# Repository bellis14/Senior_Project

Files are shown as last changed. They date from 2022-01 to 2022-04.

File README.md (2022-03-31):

# Senior Project - Personal Camerabot

* [Android Studio Setup and App Installation](https://github.com/bellis14/Senior_Project/blob/main/SoftwareSetup.md)
* [Project Specifications](https://github.com/bellis14/Senior_Project/blob/main/ProjectRequirements.md)
* [Future Development](https://github.com/bellis14/Senior_Project/blob/main/Future%20Developments.md)

### Useful Links

* [The code for the ios app and android app were found from here.](https://github.com/googlesamples/mlkit)

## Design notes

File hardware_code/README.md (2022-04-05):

# Hardware code

## Description
* The AutoCameraMan arduino file is the code that is downloaded onto the ESP32 to run the project. This file is used to broadcoast bluetooth classic to an android phone. This code successfully connects to the AutoCameraMan app and will receive motor instructions when the app is set to facial or pose detection. When the instructions are received the code will function with good motor control. iPhone devices can also connect to bluetooth classic. 
* The BLE_Server file is used to broadcoast a bluetooth low energy signal. iPhone and Android can connect to both bluetooth low energy (BLE) and bluetooth classic. Bluetooth classic is easier to implement than BLE.   

## Research 
* [Bluetooth/ESP32 Research](https://docs.google.com/document/d/1fT-Hv9j815ZINsvS9MvsHoMjV4GRWzmnJF0-fi07Mzs/edit)
* [Servo DS3225 spec sheet](https://dsservo.com/en/d_file/RDS3225%20datasheet.pdf)
* [Wiring Diagram of board and servos. Scroll down till you see it](https://create.arduino.cc/projecthub/zee9309/presentation-slide-switcher-bot-36b8f6)

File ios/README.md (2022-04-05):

# Description
The iphone portion of the project has been nearly untouched. We were able to build and run the project provided by googles ML kit but we haven't added any additional functionality. We found the resources that will be used to implement bluetooth, which can be found below in the Bluetooth Resources section, but we never integrated it into the app or even tested the bluetooth code provided by apple. The instructions for building and running the app are provided below in the Steps for setting up development on mac computer section. After you get the app running on your iphone you can start adding the other functionalities. 

# Setting up for Development 
We did the development for the iphone app on xcode which requires macOS. If you don't have a mac computer then you can either set up a virtual machine using virtualbox or VMware workstation. You can also attempt to dual boot macOS onto the computer you are currently using. You just need to make sure your laptop meets the requirements for this option. The other option is to use the mac lab down in the library. There is a way to configure virtualbox and VMware to perform more smoothly but when we attempted to use it the performance was really bad in terms of their being lag. You would try to move your mouse somewhere and it would take a solid five seconds to move. The drawback of using the mac lab is you can't use sudo commands to download stuff. If you need to download something you will have to find a work around that doesn't require sudo. As of now the IT department has revoked admin access which means you can't download xcode. It is currently downloaded on computer 4 in the mac lab if you want to use that one. That is the computer that was used for development.

## Steps for setting up development on mac computer
At the end of this setup you should be able to build and run the app on your iphone device. This means you are ready to begin adding the functionality of bluetooth. There is a link down below in the section labeled Bluetooth Resources. Go to the link in that section and hit the download button. This will download the code that apple offers to connect to bluetooth classic devices.  
* Download Xcode
* Download cocoapods. Use homebrew not gem.
  * Download Homebrew with these commands. You can find the same commands [here](https://docs.brew.sh/Installation#untar-anywhere)
    * mkdir homebrew && curl -L https://github.com/Homebrew/brew/tarball/master | tar xz --strip 1 -C homebrew
    * Add the path: export PATH="/Users/coolasacucumber/Downloads/homebrew/bin:$PATH" (You will have to run this command any time you want to run pod install and you closed the terminal)
    * The path above will be different for you. I decided to make the homebrew directory in the downloads folder. 
    * eval "$(homebrew/bin/brew shellenv)"
    * brew update --force --quiet
    * chmod -R go-w "$(brew --prefix)/share/zsh"
  * brew install cocoapods (This will take forever just fyi)
* Use cocoapods to import the dependencies in the Podfile
  * Clone the senior project repository into your workspace
  * Change into the ios directory of the repository.
  * run the command: pod install
* Setting up your iphone device
  * Do not use the iOS simulators if you are using M1 chip mac computers. Feel free to try it. If it works great!
  * Follow this [video](https://www.youtube.com/watch?v=bqh6YaMxgbE) setting up your iphone device. 
  * If after setting up the device you get this error when trying to run the app: 
  
     "Showing Recent Messages Failed to register bundle identifier: The app identifier "com.google.mlkit.quickstart.VisionExample" cannot be registered to your development team because it is not available. Change your bundle identifier to a unique string to try again." 
  
     then you need to go into the targets and select the Signings and Capabilities tab and change the Build Identifier from com.google.mlkit.quickstart.VisionExample to something different. I changed it to com.google.mlkit.quickstart.VisionExample222 and hit the try again button. After that it worked for me and then I was able to finish setting up the iphone device by going into the iphones settings >general>VPN & Device Management and then selecting the developer app as was mentioned in the above video. After this last step you should be able to run the app successfully.

## Debugging for setting up development on mac lab computers
https://alexandernadein.medium.com/undefined-symbols-and-where-to-find-them-b98f16f5f805
https://githubhot.com/repo/googlesamples/mlkit/issues/398
https://developer.apple.com/forums/thread/130493
https://developer.apple.com/forums/thread/130493

## Setting up virtual machine
* [iOS development setup using a virtual machine on VMware workstation](https://www.youtube.com/watch?v=-5FpROxjHsw)

# Bluetooth Resources
* Download [this](https://developer.apple.com/documentation/corebluetooth/using_core_bluetooth_classic). Its apples code for connecting bluetooth devices.

# ML Kit Vision Quickstart Sample App

## Introduction

This ML Kit Vision iOS Quickstart app demonstrates how to use and integrate various vision based ML Kit features into your app.

## Feature List

Features that are included in this demo app:
* [Object Detection](https://developers.google.com/ml-kit/vision/object-detection/ios) - Detect, track, and classify objects in real time and static images
* [Custom Object Detection (Birds)](https://developers.google.com/ml-kit/vision/object-detection/custom-models/ios) - Detect, track, and classify birds with a custom TensorFlow Lite model
* [Face Detection](https://developers.google.com/ml-kit/vision/face-detection/ios) - Detect faces in real time and static images
* [Text Recognition](https://developers.google.com/ml-kit/vision/text-recognition/v2/ios) - Recognize text in real time and static images
* [Barcode Scanning ](https://developers.google.com/ml-kit/vision/barcode-scanning/ios)- Scan barcodes in real time and static images
* [Image Labeling](https://developers.google.com/ml-kit/vision/image-labeling/ios) - Label images in real time and static images
* [Custom Image Labeling (Birds)](https://developers.google.com/ml-kit/vision/image-labeling/custom-models/ios) - Label images of birds with a custom TensorFlow Lite model
* [Pose Detection](https://developers.google.com/ml-kit/vision/pose-detection/ios) - Detect the position of the human body in real time.
* [Selfie Segmentation](https://developers.google.com/ml-kit/vision/selfie-segmentation/ios) - Segment people from the background in real time.

## Getting Started

* Run the sample code on your iOS device or simulator
* Try extending the code to add new features and functionality

## How to use the app

This app supports two usage scenarios: Live Camera mode and Static Image mode.

### Static Image Scenario
When the app is first opened, you will begin in Static Image mode. Use the carousel to select a specific API and hit “detect” to exercise the API on the preloaded images. In order to add your own images from the camera roll, select the camera roll icon on the top of the screen.

### Live Camera Scenario
This mode uses the camera preview as input instead of static images. In order to enter this mode, select the video camera icon in the top right corner of the screen.

## Support
-------

- [Stack Overflow](https://stackoverflow.com/questions/tagged/google-mlkit)

License
-------

Copyright 2020 Google, Inc.

Licensed to the Apache Software Foundation (ASF) under one or more contributor
license agreements.  See the NOTICE file distributed with this work for
additional information regarding copyright ownership.  The ASF licenses this
file to you under the Apache License, Version 2.0 (the "License"); you may not
use this file except in compliance with the License.  You may obtain a copy of
the License at

  http://www.apache.org/licenses/LICENSE-2.0

Unless required by applicable law or agreed to in writing, software
distributed under the License is distributed on an "AS IS" BASIS, WITHOUT
WARRANTIES OR CONDITIONS OF ANY KIND, either express or implied.  See the
License for the specific language governing permissions and limitations under
the License.

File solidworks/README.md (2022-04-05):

# SolidWorks
* If you are not familiar with SoidWorks, please review the following materials before opening the files
* [SolidWorks Configuration Help Webpage](https://help.solidworks.com/2020/English/SolidWorks/sldworks/c_Configurations_Overview.htm)
* [SolidWorks Display States Help Webpage](https://help.solidworks.com/2020/English/SolidWorks/sldworks/c_display_states_configurations_parts.htm)
* Suppressing or removing any part of assembly will immediately cause errors to both assembly solid model and drawing
* If you are not an intermidate level SolidWorks user, do not modify the SolidWorks model. Instead, use it as is.

* The SolidWorks cad file (ASSY_IRT_PT_CAM.SLDASM) has 4 different configurations

* 45 DEGREE ASSY configuration
* DEFAULT ASSY configuration
* FIXED configuration
* ROTATABLE configuration

* 45 DEGREE ASSY configuration contains Exploded View 1 and 2
* Exploded View 1 is to show an assembly between rotating table and main tilt bracket
* Exploded View 1 must use "Display State- TILT TO RT TABLE ASSY"
* Exploded View 2 is to show an assembly between the assembled tilt bracket to base
* Exploded View 2 must use "Display State - TILT TO BASE ASSY"

* DEFAULT ASSY configuration
* Exploded View 3 is to show an assembly between the tilt bracket to tilt servo
* Exploded View 3 must use "Display Sate-TILT TO SERVO SIDE BRKT ASSY"
* Exploded View 4 is to show an assembly between combined previous assembly and battery base
* Exploded View 4 must use "Display State-MAIN BASE TO BATTERY BASE ASSY"

* FIXED configuration shows the entire assembly and tilt bracket is not rotatable

* ROTATABLE configuration shows the entire assembly and tilt bracket & phone craddle bracket are rotatable

* All fastener solid models are donwloaded from McMaster-Carr website (https://www.mcmaster.com/)
* Most fasteners are assembled using FEATURE DRIVEN PATTERN in SolidWorks
* Thus, suppressing or removing fasteners will cause errors.
* Please be familiar with SolidWorks FEATURE DRIVEN PATTERN assembly before modifying the solid model
* [SolidWorks Feature Driven Pattern Assembly Help Webpage](https://help.solidworks.com/2012/English/SolidWorks/sldworks/HIDD_DVE_COMPPAT_DERIVED.htm)

* PROTOTYPE DEVELOPMENT ARCHIVE folder has the entire history of solid model design from the begining to end

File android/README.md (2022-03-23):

# ML Kit Vision Quickstart Sample App

## Introduction

This ML Kit Quickstart app demonstrates how to use and integrate various vision based ML Kit features into your app.

## Feature List

Features that are included in this Quickstart app:
* [Object Detection](https://developers.google.com/ml-kit/vision/object-detection/android) - Detect, track, and classify objects in real time and static images
* [Face Detection](https://developers.google.com/ml-kit/vision/face-detection/android) - Detect faces in real time and static images
* [Text Recognition](https://developers.google.com/ml-kit/vision/text-recognition/android) - Recognize text in real time and static images
* [Barcode Scanning](https://developers.google.com/ml-kit/vision/barcode-scanning/android)  - Scan barcodes in real time and static images
* [Image Labeling](https://developers.google.com/ml-kit/vision/image-labeling/android) - Label images in real time and static images
* [Custom Image Labeling - Birds](https://developers.google.com/ml-kit/vision/image-labeling/custom-models/android) - Label images of birds with a custom TensorFlow Lite model.
* [Pose Detection](https://developers.google.com/ml-kit/vision/pose-detection/android) - Detect the position of the human body in real time.
* [Selfie Segmentation](https://developers.google.com/ml-kit/vision/selfie-segmentation/android) - Segment people from the background in real time.

   

## Getting Started

* Run the sample code on your Android device or emulator
* Try extending the code to add new features and functionality

## How to use the app

This app supports three usage scenarios: Live Camera, Static Image, and CameraX enabled live camera.

### Live Camera scenario
It uses the camera preview as input and contains these API workflows: Object detection & tracking, Face Detection, Text Recognition, Barcode Scanning, Image Labeling, and Pose Detection. There's also a settings page that allows you to configure several options:
* Camera
    * Preview size - Specify the preview size of rear/front camera manually (Default size is chosen appropriately based on screen size)
    * Enable live viewport - Toggle between blocking camera preview by API processing and result rendering or not
* Object detection / Custom Object Detection
    * Enable multiple objects -- Enable multiple objects to be detected at once
    * Enable classification -- Enable classification for each detected object
* Face Detection
    * Landmark mode -- Toggle between showing no or all facial landmarks
    * Contour mode -- Toggle between showing no or all contours
    * Classification mode -- Toggle between showing no or all classifications (smiling, eyes open/closed)
    * Performance mode -- Toggle between two operating modes (Fast or Accurate)
    * Face tracking -- Enable or disable face tracking
    * Minimum face size -- Choose the proportion of the head width to the image width
* Pose Detection
    * Performance mode -- Allows you to switch between "Fast" and "Accurate" operation mode
    * Show in-frame likelihood -- Displays InFrameLikelihood score for each landmark
    * Visualize z value -- Uses different colors to indicate z difference (red: smaller z, blue: larger z)
    * Rescale z value for visualization -- Maps the smallest z value to the most red and the largest z value to the most blue. This makes z difference more obvious
    * Run classification -- Classify squat and pushup poses. Count reps in streaming mode.
* Selfie Segmentation
    * Enable raw size mask -- Asks the segmenter to return the raw size mask which matches the model output size.

### Static Image scenario
The static image scenario is identical to the live camera scenario, but instead relies on images fed into the app through the gallery.

### CameraX Live Preview scenario
The CameraX live preview scenario is very similar to the native live camera scenario, but instead relies on CameraX live preview. Note: CameraX is only supported on API level 21+.

## Support

* [Documentation](https://developers.google.com/ml-kit/guides)
* [API Reference](https://developers.google.com/ml-kit/reference/android)
* [Stack Overflow](https://stackoverflow.com/questions/tagged/google-mlkit)

## License

Copyright 2020 Google, Inc.

Licensed to the Apache Software Foundation (ASF) under one or more contributor
license agreements.  See the NOTICE file distributed with this work for
additional information regarding copyright ownership.  The ASF licenses this
file to you under the Apache License, Version 2.0 (the "License"); you may not
use this file except in compliance with the License.  You may obtain a copy of
the License at

  http://www.apache.org/licenses/LICENSE-2.0

Unless required by applicable law or agreed to in writing, software
distributed under the License is distributed on an "AS IS" BASIS, WITHOUT
WARRANTIES OR CONDITIONS OF ANY KIND, either express or implied.  See the
License for the specific language governing permissions and limitations under
the License.

# Video / Audio Recording Resources
One major pillar of this application is the ability to record a video while the application is tracking a face.
The purpose of writing this is to document how that was accomplished as well as the various issues that were encounter along the way so as to help future developers better understand the task at hand.

## The Goal
The goal when we set out was to create an application that could track a face or person while recording video in the background. Below will outline the various ways the internet has attempted to solve this issues as well as the solution that was implemented here. 

## Standard Video Recording
https://developer.android.com/training/camera/videobasics This is a link to Android official documentation that outlines the standard way to record video. This does not work in this specific application and the reason this does not is because it hijacks the camera from the core functionality of the application. It essentially switches to a new application temporarily pausing everything else.

## MediaRecorder Solution
https://developer.android.com/guide/topics/media/mediarecorder This link is androids second more involved way of recording video. This solution works for audio recording because no other part of the code is using the microphone, so complete control of the microphone does not affect the rest of the application. This however does not work for video recording for a similar reason as the standard recording solution. Trying to record video with the media recorder also steal the camera from the core application functionality eliminating its ability to preform any type of image recognition. 

## Present Solution
The current solution has been to use the MediaRecorder object to record sound on a background thread while at the same time saving frames already being captured by the camera for image recognition. This solution involves two threaded classes that interface to Runnable: StopRecordingRunnable and StartRecordingRunnable. These handle the starting and stopping of the audio recording as well as the creation of the video. 
The creation of the video involves taking the frames that have been saved to a unique directory within the phones storage, and taking the most recent audio recording and putting them together using a library called FFmpeg. Documentation and links are below. The following objects and methods are used in this process and can be studied to gain a better understanding of how this whole process works. 

### LivePreviewActivity
-	recordButton.setOnClickListener
This is the logic that handels the record button toggling from white to red. As well as kick off the video recording functionality by creating a StartRecordingRunnable thread and starting it.

### StartRecordingRunnable
-	This object is responsible for setting a recording flag that exists in CameraSource, and setting up the media Recorder object for audio and starting it. 
### StopRecordingRunnable
-	This object is responsible for bringing it all together. It releases the recording flag to signal CameraSource to stop saving frames. It releases the mediaRecorder to stop recording audio, and it takes the frames and audio and creates a binary executable that is used by FFmpeg to create a final video. It also cleans up memory by deleting all of the frames after the video is created.
### CameraSource
-	This object is a major component of the core functionality of the application. It is responsible for setting up the camera for use by the application. This is why the camera frames are saved here. 
-	onPreviewFrame This method is a part of the camera hardware and is called every time the camera has a new frame. This method checks to see if the recording flag is true and if it is it passes the frame in the form of a byte array to the SaveImage method. 
-	SaveImage this method takes a byte array and converts it into a YuvImage. The YuvImage is then converted into a bitmap, then creates a matrix to rotate the bitmap 90 degrees, then the bitmap is converted into a jpg to be saved. There is probably a better way to do this but this is what worked. 
-	In CameraSource ther is a global variable numFrames, this variable is important because it keeps track of the number of frames that are saved during a recording session. This is needed to save the frames in numerical order as well as to calculate the frame rate to be used in video creation later.
### FFmpeg
-	This library is added in the manifests file and is used to create a video with the file of frames that are saved when the record button is pushed. 
-	Below are useful links for using FFmpeg
-	https://www.geeksforgeeks.org/how-to-use-ffmpeg-in-android-with-example/
-	https://github.com/tanersener/mobile-ffmpeg
-	https://codingpoint.tech/how-to-use-ffmpeg-in-android/
- https://ffmpeg.org/

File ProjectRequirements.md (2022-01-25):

# Project Requirements:

## General Requirements:
### Primary - 
* Phone mount tripod attachment with motorized pan and tilt capabilities
* The mount receives signals (via bluetooth) to control the the pan and tilt angles
* A mobile app uses image recognition to generate these angles 
* The app keeps a detected object in frame via physical pan and tilt adjustments

### Secondary -
* Phone mount uses 4 or more integrated sound sensors/microphones to detect positional sound
* App has a sound mode that moves the phone in the direction of a desired sound
* The App uses voice recognition to prioritize phone's position

## Hardware Requirements:
### Primary -
* Motors receive a signal from controller (Arduino) to change angle
* Motor sound does not significantly disrupt phone audio recording
* Motors can rotate mount with phone (0.4-1.0 lb) in quick and precise movements
* Tripod mount can tilt 90 degrees (up and down)
* Tripod mount can pan 180-360 (side to side)

### Secondary -
* Mount can record audio using integrated microphones

## Software Requirements (General):
### Primary - 
* App can record video
* App uses image recognition to identify key objects and tracks bounding vertices
* App uses bounding vertices of object and generates pan and tilt angles
* App connects via bluetooth to phone mount control board
* App can send pan and tilt angles to the mount controller

## Software Requirements (Object Tracking) -
### Primary -
* App can track a human face
* App can track a body

### Secondary - 
* App can learn a specific object/person/face to track
* App uses pose detection to predict future position of person to reduce latency

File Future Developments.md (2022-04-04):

# Potential Future Developments

## User Interface
* UI has 2 modes you select from at startup; face (<6 ft away) and pose (>6 ft away)

## Optimization
* Research [hardware configuration](https://developers.google.com/android/reference/com/google/mlkit/vision/pose/PoseDetectorOptionsBase) for possible performance improvements
* Reduce resolution of image being processed for face/pose detection (while maintaining resolution for recording)
* **Create seperate thread to enable recording without drastically decreasing performance**

## Additional Features
* On device microphones that enable device to [look towards the loudest sound](https://www.youtube.com/watch?v=CgrFabQvES4) in the event the camera fails to find a person over a period of time (allows user to clap loudly or shout "HEY!" for the camera to find it)
* Gesture/voice controls (ie. hand gestures to start/stop recording)
* Create the same app but on iOS for iPhones. The repository includes the code and documentation for setting up/building the ios code on xcode but no additional features like bluetooth have been added to it, so it's a blank canvas really. 
* Have a device to a person carries on them and the camera mount will follow that device around wherever it goes.

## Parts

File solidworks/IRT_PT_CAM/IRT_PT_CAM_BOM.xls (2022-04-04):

ITEM NO. | PART NUMBER | DESCRIPTION | QTY. | MANUFACTURER | MANUFACTURER PART NUMBER | DISTRIBUTOR PART NUMBER | LINK (DISTRIBUTOR) | ESTIMATE COST
1 | PAN_BASE_MAIN | MAIN BASE (3D PRINTED ABS) | 1 | N/A | N/A | N/A | N/A | $10.98
2 | SPACER_0.75 DIA_8MM | SPACER (3D PRINTED ABS) | 4 | N/A | N/A | N/A | N/A
3 | 20KG_6.8V_8V_DIGITAL_SERVO_DSSERVO | ANNIMOS 25KG DIGITAL SERVO | 2 | ANNIMOS | DS3225MG | B07GK1G5FV | https://www.amazon.com/gp/product/B07GK1G5FV/ref=ox_sc_act_title_2?smid=A3NMC7084N0TIJ&psc=1 | $19.78
4 | TURNTABLE_ROTATING_ASSY | ROTATING TABLE W/ BEARING | 1 | TROOPS BBQ | N/A | B07GY55MYT | https://www.amazon.com/gp/product/B07GY55MYT/ref=ox_sc_act_title_1?smid=A2ZKGRENV5NC9J&th=1 | $9.54
5 | HORN_SERVO | M3 THREADED SERVO HORN | 2 | N/A | N/A | N/A | N/A | N/A
6 | TILT_MAIN_BRACKET | TILT BRACKET (3D PRINTED ABS) | 1 | N/A | N/A | N/A | N/A | $25.56
7 | INNER_COVER_20KG_6.8V_8V_DIGITAL_SERVO_DSSERVO | COVER (3D PRINTED ABS) | 1 | N/A | N/A | N/A | N/A | $6.00
8 | MOCKUP_LONG_HORN_SERVO | SHAFT (3D PRINTED ABS) | 1 | N/A | N/A | N/A | N/A
9 | TILT_LONG_BRACKET | PHONE CRADDLE (3D PRINTED ABS) | 1 | N/A | N/A | N/A | N/A
10 | COVER_20KG_6.8V_8V_DIGITAL_SERVO_DSSERVO | OUTER COVER (3D PRINTED ABS) | 1 | N/A | N/A | N/A | N/A
11 | BATTERY_POWER_MASTER_GPCT669 | POWER MASTER 1.2 AMP BATTERY BANK USB CHARGER | 1 | GPCT | GPCT | N/A | https://www.walmart.com/ip/PowerMaster-12000mAh-Portable-Charger-with-Dual-USB-Ports-3-1A-Output-Power-Bank-Black/148893943 | $29.07
12 | BASE_BATTERY_ESP32 | LOWER BASE BATTERY ESP32 STORAGE | 1 | N/A | N/A | N/A | N/A | $14.44
13 | PUSH_DOWN | PUSH DOWN BRACKET M4 SC CLEARANCE THRU HOLE | 4 | N/A | N/A | N/A | N/A
14 | ESP32 | CONTROL BOARD BLUETOOTH CAPABLE 3.3V | 1 | Espressif Systems | ESP32-DEVKITC-32D | 1965-1000-ND | https://www.digikey.com/en/products/detail/espressif-systems/ESP32-DEVKITC-32D/9356990 | $18.65
15 | TRIPOD_ADAPTER | TRIPOD ADAPTER 3 X 3 W/ 1/4-20 HOLE | 1 | N/A | N/A | N/A | N/A
16 | 90592A090 | M4 Steel Hex Nut | 16 | McMASTER-CARR | 90592A090 | 90592A090 | https://www.mcmaster.com/ | $2.40
17 | 90592A085 | M3 Steel Hex Nut | 9 | McMASTER-CARR | 90592A085 | 90592A085 | https://www.mcmaster.com/ | $1.35
18 | 98689A112 | M3 General Purpose 18-8 Stainless Steel Washer | 8 | McMASTER-CARR | 98689A112 | 98689A112 | https://www.mcmaster.com/ | $1.20
19 | 92095A184 | M3 X 16MM Button Head Hex Drive Screw | 4 | McMASTER-CARR | 92095A184 | 92095A184 | https://www.mcmaster.com/ | $0.60
20 | 91292A113 | M3 X 10MM 18-8 Stainless Steel Socket Head Screw | 4 | McMASTER-CARR | 91292A113 | 91292A113 | https://www.mcmaster.com/ | $0.60
21 | 91292A114 | M3 X 12MM 18-8 Stainless Steel Socket Head Screw | 5 | McMASTER-CARR | 91292A114 | 91292A114 | https://www.mcmaster.com/ | $0.75
22 | 91292A116 | 18-8 Stainless Steel Socket Head Screw | 4 | McMASTER-CARR | 91292A116 | 91292A116 | https://www.mcmaster.com/ | $0.60
23 | 91292A038 | M4 X 14MM 18-8 Stainless Steel Socket Head Screw | 4 | McMASTER-CARR | 91292A038 | 91292A038 | https://www.mcmaster.com/ | $0.60
24 | 90128A214 | M4 X 12MM Zinc-Plated Alloy Steel Socket Head Screw | 4 | McMASTER-CARR | 90128A214 | 90128A214 | https://www.mcmaster.com/ | $0.60
25 | 91292A112 | M3 X 8MM 18-8 Stainless Steel Socket Head Screw | 6 | McMASTER-CARR | 91292A112 | 91292A112 | https://www.mcmaster.com/ | $0.90
26 | 91292A132 | M4 X 40MM 18-8 Stainless Steel Socket Head Screw | 4 | McMASTER-CARR | 91292A132 | 91292A132 | https://www.mcmaster.com/ | $0.60
27 | 92673A113 | 1/4-20 18-8 Stainless Steel Hex Nut | 1 | McMASTER-CARR | 92673A113 | 92673A113 | https://www.mcmaster.com/ | $0.15
28 | 91274A160 | 1/4-20 X 5/8" Zinc-Aluminum-Coated Alloy Steel Socket Head Screw | 1 | McMASTER-CARR | 91274A160 | 91274A160 | https://www.mcmaster.com/ | $0.15
29 | INSERT_PUSH_DOWN | PUSH DOWN BRACKET THREAD COVER (3D PRINTED) | 4 | N/A | N/A | N/A | N/A
30 | INSERT_CENTER_PUSH_DOWN | CENTER BASE 1/4-20 SCREW COVER (3D PRINTED) | 1 | N/A | N/A | N/A | N/A
999-1 | ANDROID APP. |  | N/A | N/A | N/A | N/A | N/A
999-2 | ANDROID APP. INSTALLATION & OPERATION MANUAL |  | N/A | N/A | N/A | N/A | N/A
999-3 | MECHANICAL ASSEMBLY DRAWING | MECHANICAL ASSY & DIMENSION DRAWINGS | N/A | N/A | N/A | N/A | N/A
999-4 | SUPER GLUE | N/A | N/A | N/A | N/A | N/A | N/A
999-5 | TOOL | M3 & M4 ALLEN WRENCH AND 1/4-20 NUT WRENCH | N/A | N/A | N/A | N/A | N/A

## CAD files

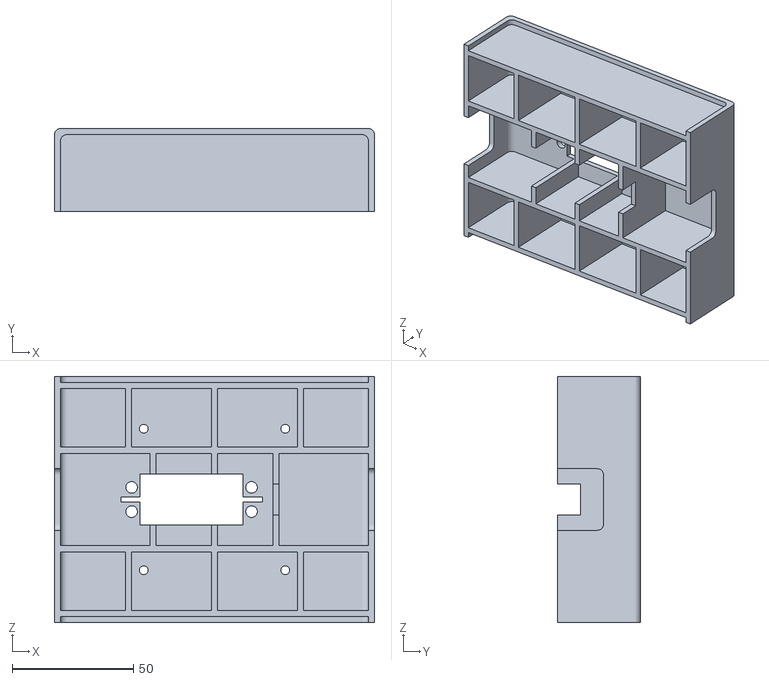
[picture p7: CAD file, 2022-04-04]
solidworks/IRT_PT_CAM/STL FILES FOR 3D PRINT/PAN_BASE_MAIN.STL
132.1 x 34.3 x 101.6

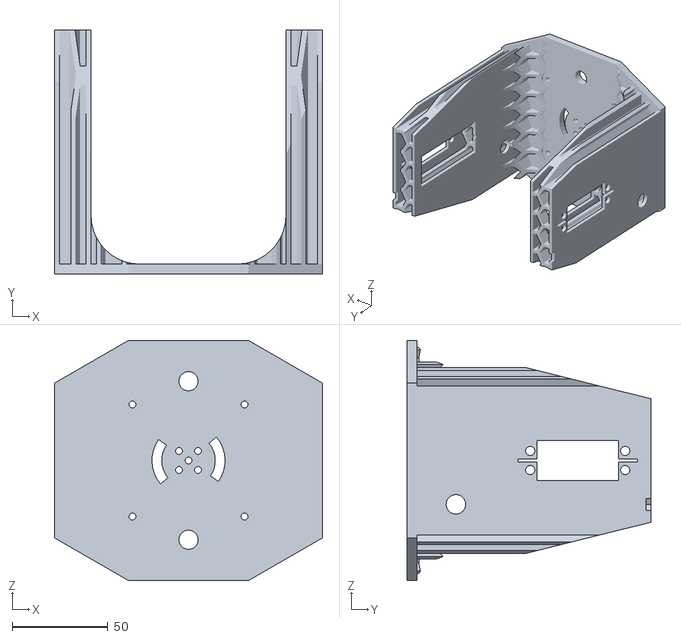
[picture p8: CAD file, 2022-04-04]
solidworks/IRT_PT_CAM/STL FILES FOR 3D PRINT/TILT_MAIN_BRACKET.STL
139.7 x 127.0 x 125.2

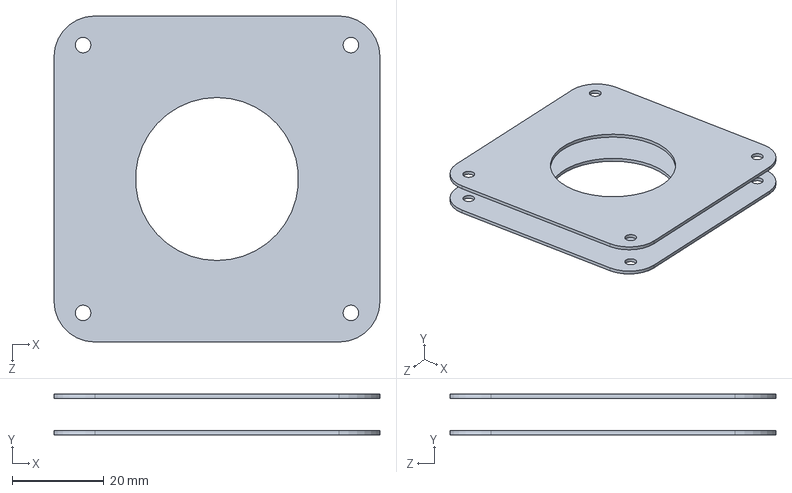
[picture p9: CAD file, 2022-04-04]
solidworks/IRT_PT_CAM/TURNTABLE_ROTATING_ASSY.SLDASM
71.1 x 8.89 x 71.1 mm
TURNTABLE_ROTATING_2.8 X 2.8 x 2

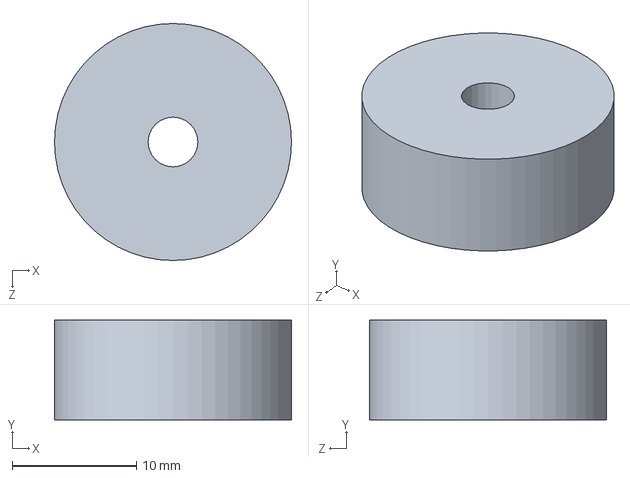
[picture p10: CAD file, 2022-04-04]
solidworks/IRT_PT_CAM/SPACER_0.75 DIA_8MM.SLDPRT
19.1 x 8.00 x 19.1 mm

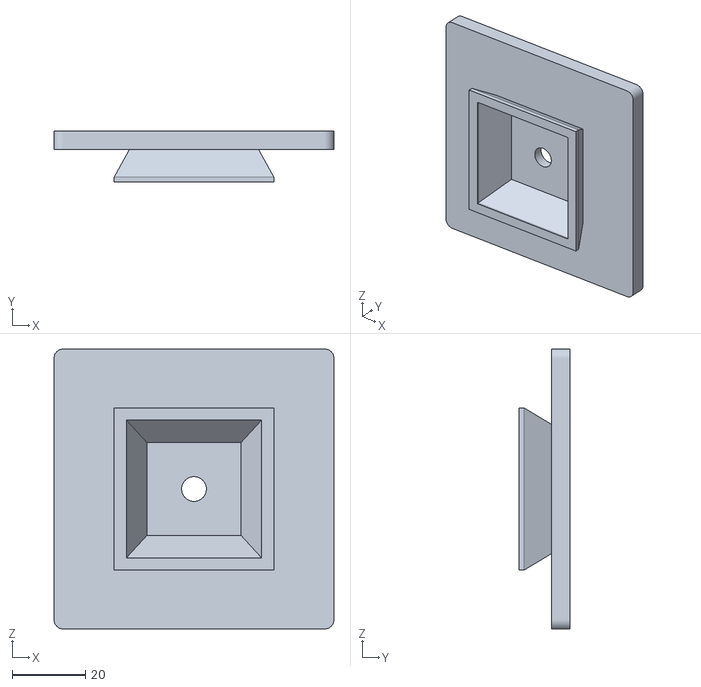
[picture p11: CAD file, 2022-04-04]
solidworks/IRT_PT_CAM/STL FILES FOR 3D PRINT/TRIPOD_ADAPTER.STL
76.2 x 14.0 x 76.2

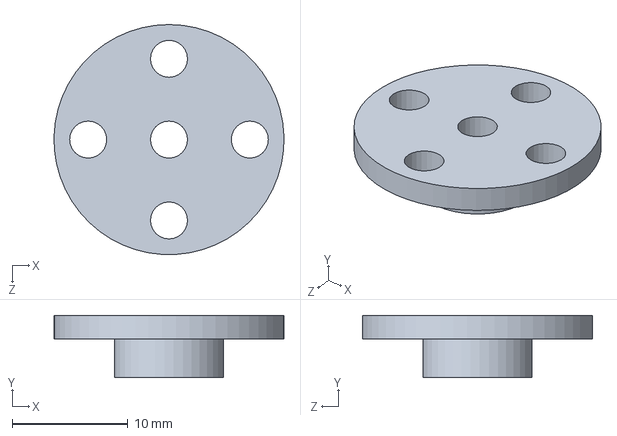
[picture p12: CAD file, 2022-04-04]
solidworks/IRT_PT_CAM/HORN_SERVO.SLDPRT
19.9 x 5.38 x 19.9 mm

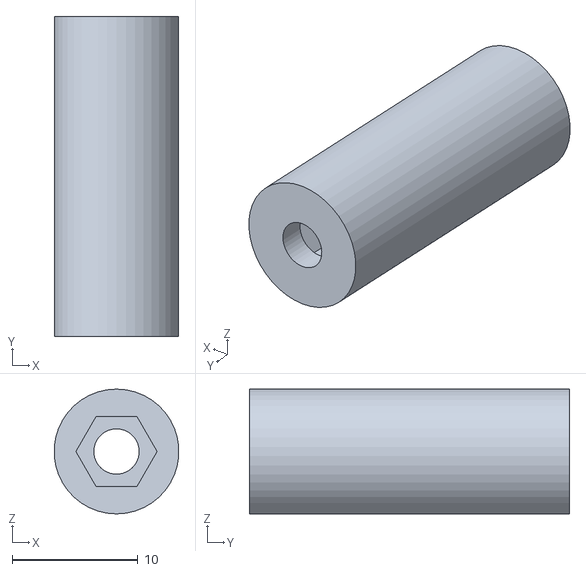
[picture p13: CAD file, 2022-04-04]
solidworks/IRT_PT_CAM/STL FILES FOR 3D PRINT/MOCKUP_LONG_HORN_SERVO.STL
9.88 x 25.4 x 9.91

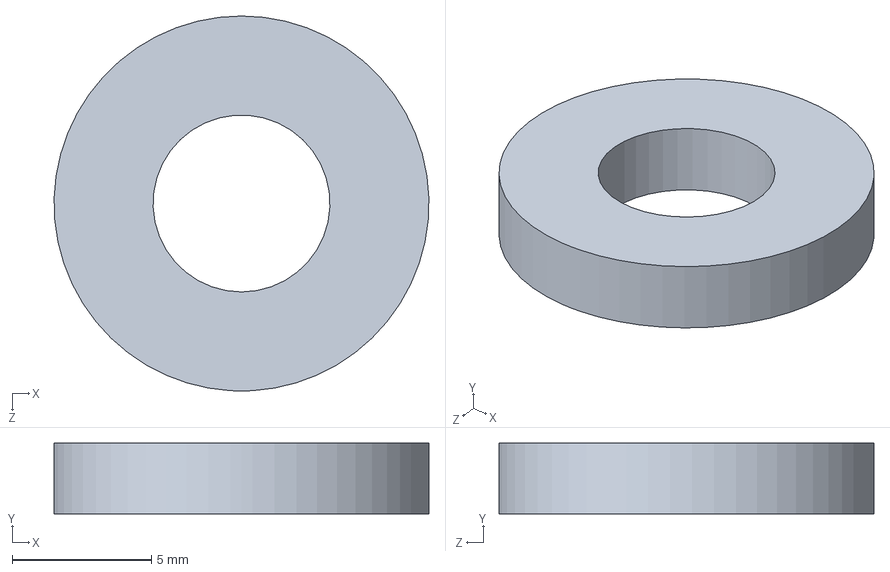
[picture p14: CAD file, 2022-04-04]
solidworks/IRT_PT_CAM/INSERT_CENTER_PUSH_DOWN.SLDPRT
13.5 x 2.54 x 13.5 mm

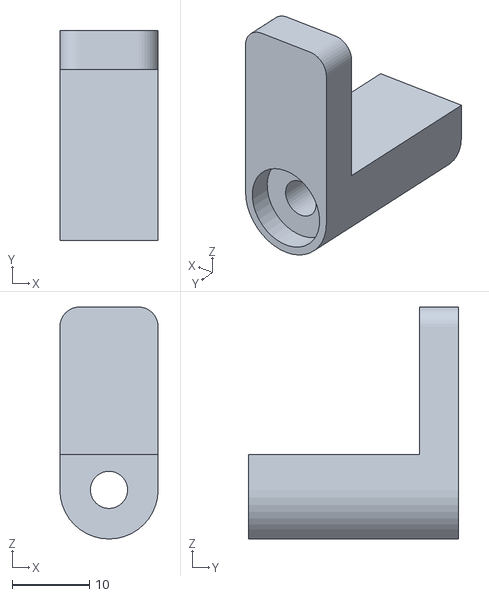
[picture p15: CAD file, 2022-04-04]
solidworks/IRT_PT_CAM/STL FILES FOR 3D PRINT/PUSH_DOWN.STL
12.7 x 27.2 x 30.0

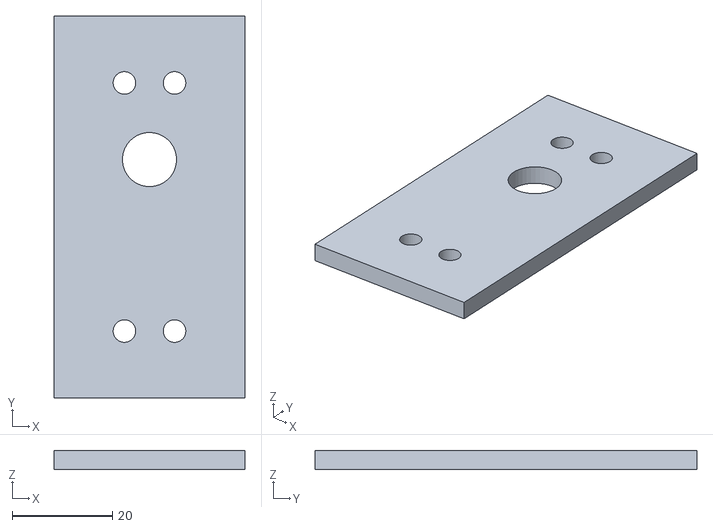
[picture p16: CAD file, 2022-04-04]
solidworks/IRT_PT_CAM/STL FILES FOR 3D PRINT/COVER_20KG_6.8V_8V_DIGITAL_SERVO_DSSERVO.STL
38.1 x 76.2 x 3.81

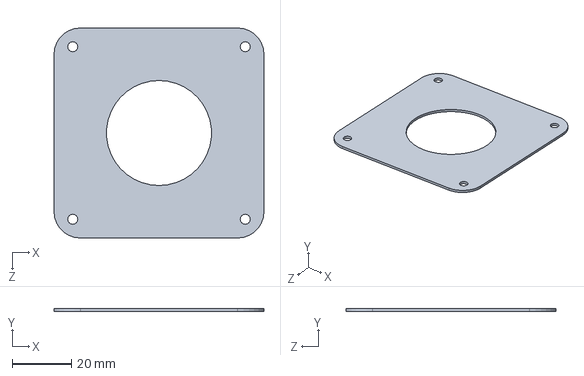
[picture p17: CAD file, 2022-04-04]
solidworks/IRT_PT_CAM/TURNTABLE_ROTATING_2.8 X 2.8.SLDPRT
71.1 x 0.952 x 71.1 mm

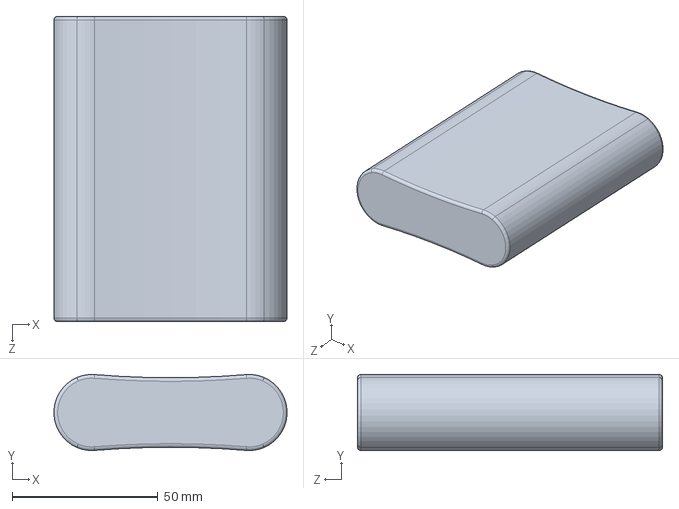
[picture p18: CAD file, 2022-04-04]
solidworks/IRT_PT_CAM/BATTERY_POWER_MASTER_GPCT669.SLDPRT
79.9 x 26.1 x 104.8 mm

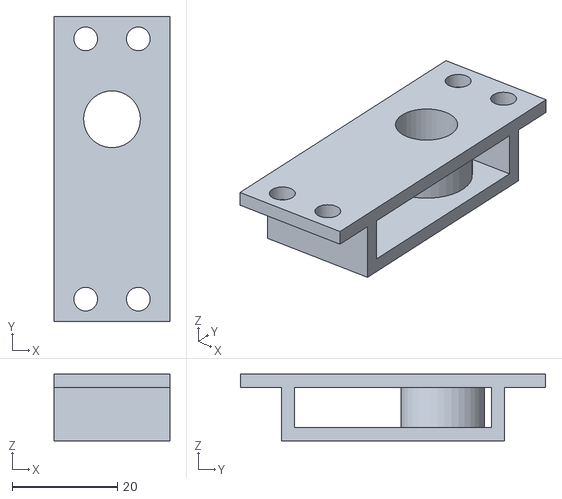
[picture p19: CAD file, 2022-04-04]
solidworks/IRT_PT_CAM/STL FILES FOR 3D PRINT/INNER_COVER_20KG_6.8V_8V_DIGITAL_SERVO_DSSERVO.STL
22.0 x 58.0 x 12.7

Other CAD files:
solidworks/IRT_PT_CAM/TURNTABLE_ROTATING_ASSY-DESKTOP-PG48QU8.SLDASM
solidworks/IRT_PT_CAM/PAN_BASE_MAIN.SLDPRT
solidworks/IRT_PT_CAM/MOCKUP_LONG_HORN_SERVO.SLDPRT
solidworks/IRT_PT_CAM/PUSH_DOWN.SLDPRT
solidworks/IRT_PT_CAM/STL FILES FOR 3D PRINT/SPACER_0.75 DIA_8MM.STL
solidworks/IRT_PT_CAM/20KG_6.8V_8V_DIGITAL_SERVO_DSSERVO.SLDDRW
solidworks/IRT_PT_CAM/20KG_6.8V_8V_DIGITAL_SERVO_DSSERVO.SLDPRT
solidworks/IRT_PT_CAM/BASE_1.3.SLDDRW
solidworks/IRT_PT_CAM/BASE_1.3.SLDPRT
solidworks/IRT_PT_CAM/BASE_BATTERY_ESP32.SLDPRT
solidworks/IRT_PT_CAM/CABLE_TIE.SLDPRT
solidworks/IRT_PT_CAM/COVER_20KG_6.8V_8V_DIGITAL_SERVO_DSSERVO.SLDPRT
solidworks/IRT_PT_CAM/ESP32.SLDDRW
solidworks/IRT_PT_CAM/ESP32.SLDPRT
solidworks/IRT_PT_CAM/Fasteners/1 4 -20 5 AND 8_Zinc-Aluminum-Coated Alloy Steel Socket Head Screw_91274A160.SLDPRT
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

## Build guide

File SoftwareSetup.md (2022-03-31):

# Android Studio Set Up and App Installation

### Install Android Studio and follow [the instructions](https://developer.android.com/studio/install)

### Clone [Repository]()
* From Android Studio select *File* -> *New* -> *Project From Version Control*
* Copy the link to clone the repository
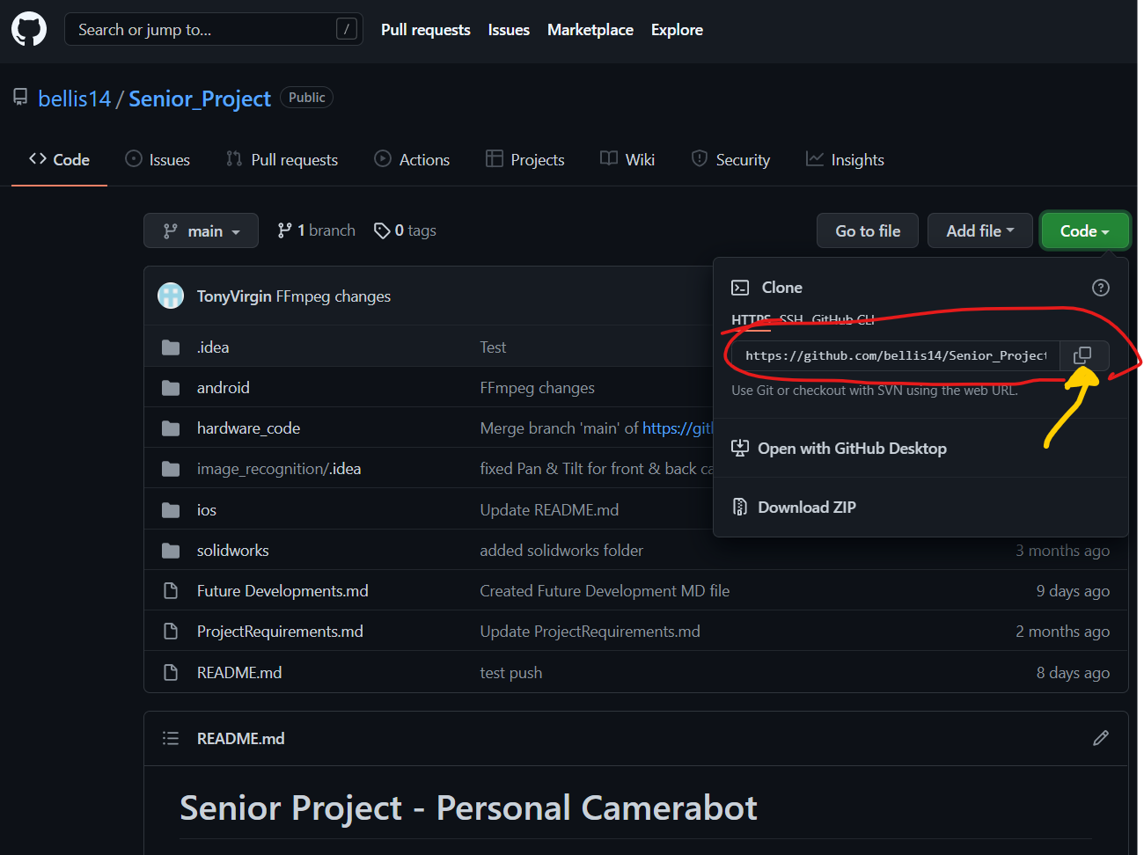
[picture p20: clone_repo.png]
Clone Repo

* Paste link in URL textbox in Android Studio

### Build the Project
* *File -> Open*
* Navigate to *android* directory and select Open
* Select the green hammer to build or go to *Build -> Make Project*

### Set up Phone
* Set phone to [Developer Mode](https://developer.android.com/studio/run/device#setting-up) 
* Connect phone to computer via USB (Your device should automatically appear in toolbar of Android Studio)
* Run 'app'

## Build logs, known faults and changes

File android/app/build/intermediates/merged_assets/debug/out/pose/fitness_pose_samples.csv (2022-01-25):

Screenshot_2021-02-11_at_12.43.07.png | pushups_up | 1251.0012 | 384.75177 | -1716.2709 | 1273.62 | 335.6524 | -1687.6895 | 1289.1946 | 333.0695 | -1687.8185 | 1305.1869 | 330.30487 | -1687.6696 | 1224.0494 | 337.55386 | -1683.0747 | 1207.5674 | 336.34988 | -1683.0284 | 1191.0675 | 335.42764 | -1682.8302 | 1327.9669 | 323.61716 | -1387.2709 | 1164.6804 | 330.69382 | -1358.8682 | 1278.6653 | 411.4735 | -1596.0863 | 1224.2347 | 412.6137 | -1587.069 | 1455.528 | 464.08652 | -1138.7732 | 1037.5433 | 483.5423 | -1115.6373 | 1612.7382 | 710.3087 | -1251.8538 | 910.18976 | 739.30524 | -1241.1416 | 1755.0282 | 991.45496 | -1415.0264 | 775.6637 | 1006.5177 | -1341.4398 | 1820.6271 | 1031.5334 | -1491.4453 | 708.1981 | 1043.5697 | -1394.7319 | 1788.2871
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

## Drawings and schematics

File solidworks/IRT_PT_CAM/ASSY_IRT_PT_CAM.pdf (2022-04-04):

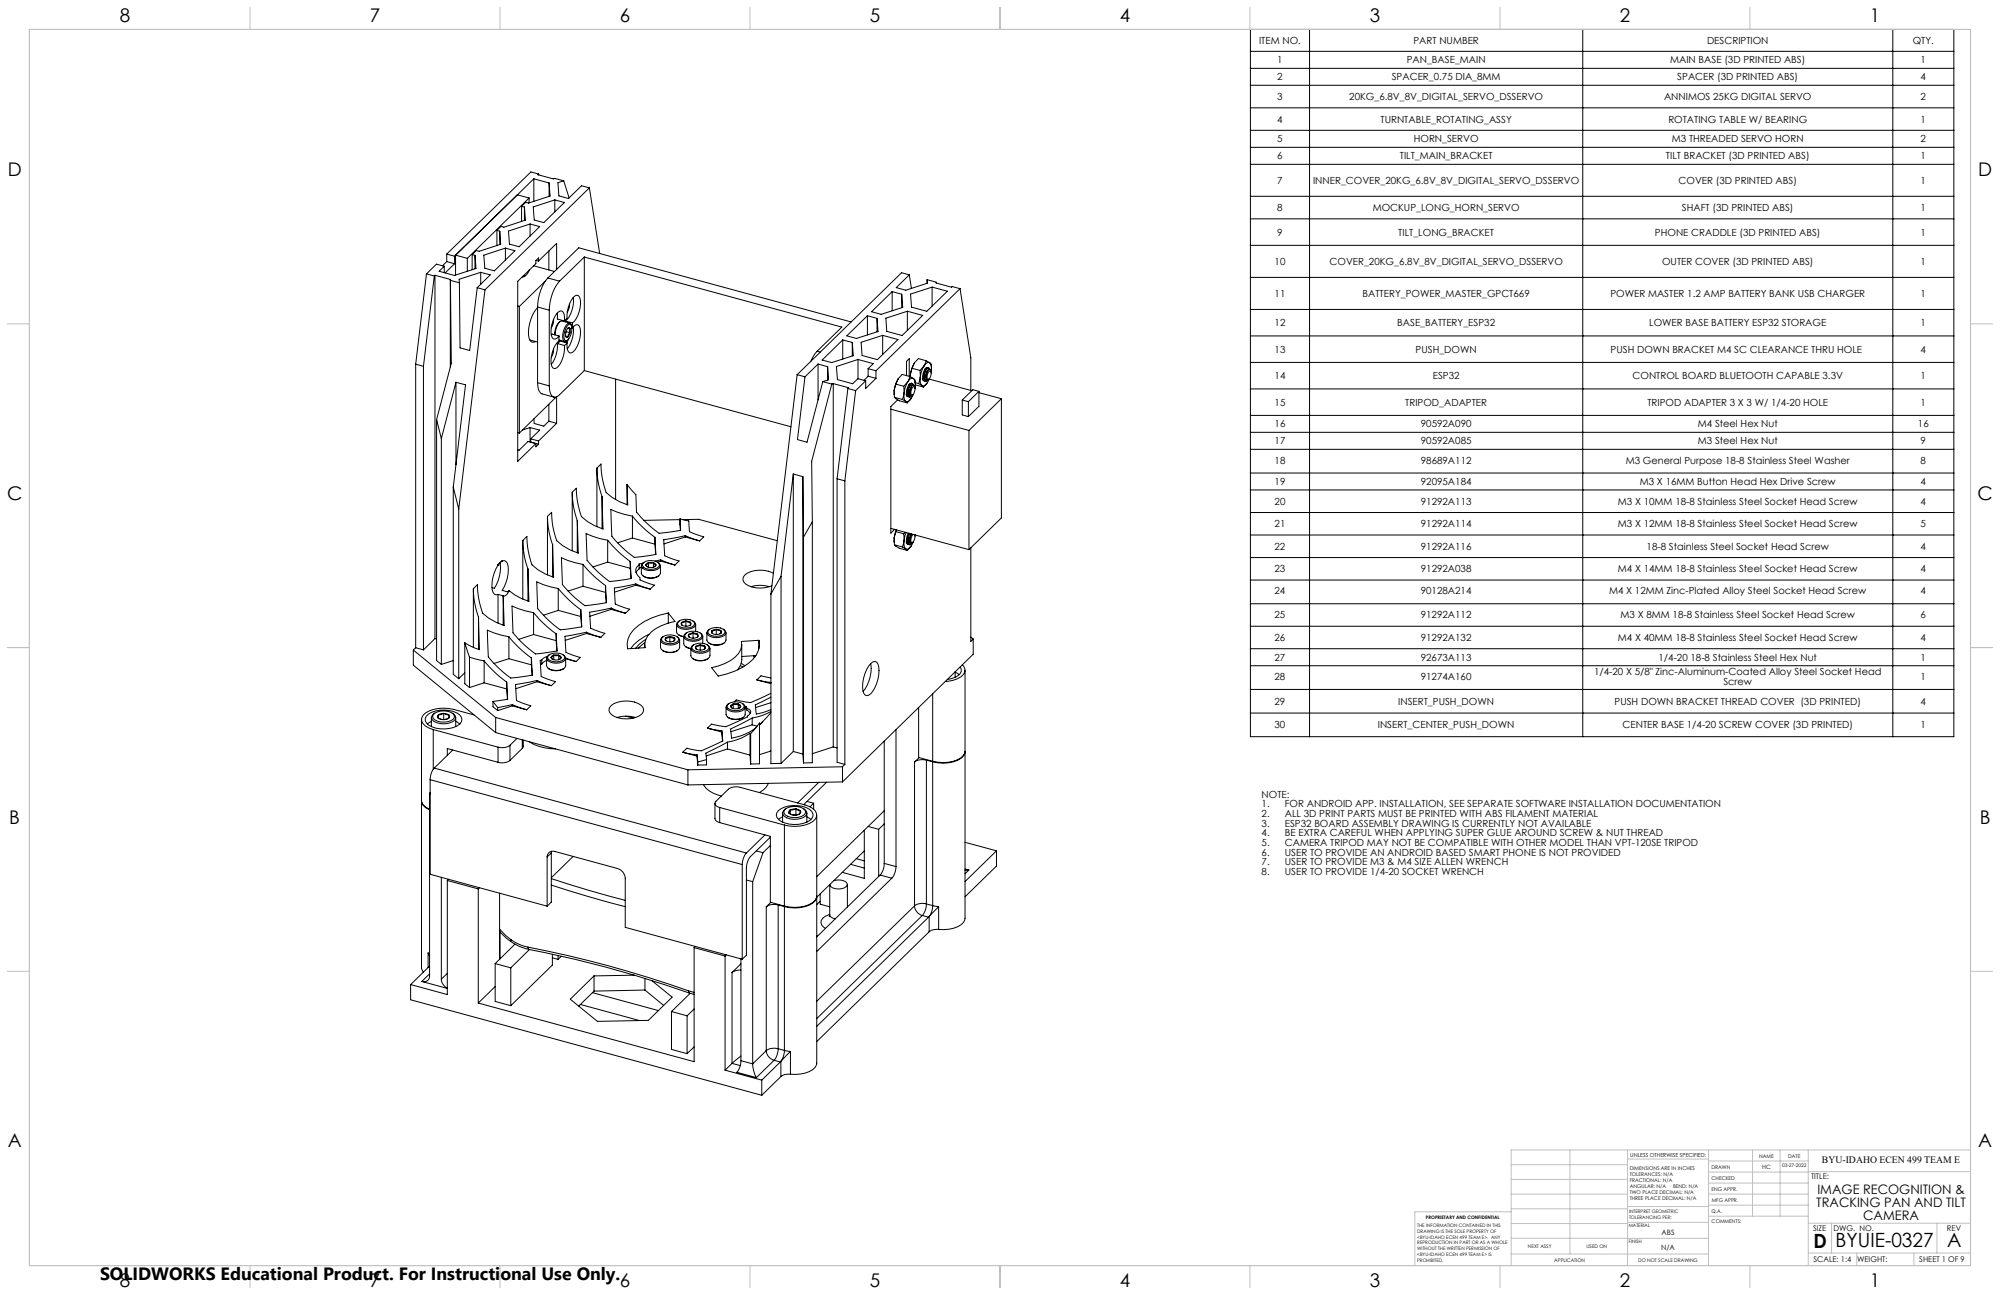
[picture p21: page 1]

ITEM NO. | PART NUMBER | DESCRIPTION | QTY.
1 | PAN_BASE_MAIN | MAIN BASE (3D PRINTED ABS) | 1
2 | SPACER_0.75 DIA_8MM | SPACER (3D PRINTED ABS) | 4
3 | 20KG_6.8V_8V_DIGITAL_SERVO_DSSERVO | ANNIMOS 25KG DIGITAL SERVO | 2
4 | TURNTABLE_ROTATING_ASSY | ROTATING TABLE W/ BEARING | 1
5 | HORN_SERVO | M3 THREADED SERVO HORN | 2
6 | TILT_MAIN_BRACKET | TILT BRACKET (3D PRINTED ABS) | 1
7 | INNER_COVER_20KG_6.8V_8V_DIGITAL_SERVO_DSSERVO | COVER (3D PRINTED ABS) | 1

8 | MOCKUP_LONG_HORN_SERVO | SHAFT (3D PRINTED ABS) | 1
9 | TILT_LONG_BRACKET | PHONE CRADDLE (3D PRINTED ABS) | 1

10 | COVER_20KG_6.8V_8V_DIGITAL_SERVO_DSSERVO | OUTER COVER (3D PRINTED ABS) | 1

11 | BATTERY_POWER_MASTER_GPCT669 | POWER MASTER 1.2 AMP BATTERY BANK USB CHARGER | 1

12 | BASE_BATTERY_ESP32 | LOWER BASE BATTERY ESP32 STORAGE | 1

13 | PUSH_DOWN | PUSH DOWN BRACKET M4 SC CLEARANCE THRU HOLE | 4

14 | ESP32 | CONTROL BOARD BLUETOOTH CAPABLE 3.3V | 1

15 | TRIPOD_ADAPTER | TRIPOD ADAPTER 3 X 3 W/ 1/4-20 HOLE | 1
16 | 90592A090 | M4 Steel Hex Nut | 16
17 | 90592A085 | M3 Steel Hex Nut | 9
18 | 98689A112 | M3 General Purpose 18-8 Stainless Steel Washer | 8
19 | 92095A184 | M3 X 16MM Button Head Hex Drive Screw | 4
20 | 91292A113 | M3 X 10MM 18-8 Stainless Steel Socket Head Screw | 4
21 | 91292A114 | M3 X 12MM 18-8 Stainless Steel Socket Head Screw | 5
22 | 91292A116 | 18-8 Stainless Steel Socket Head Screw | 4
23 | 91292A038 | M4 X 14MM 18-8 Stainless Steel Socket Head Screw | 4
24 | 90128A214 | M4 X 12MM Zinc-Plated Alloy Steel Socket Head Screw | 4
25 | 91292A112 | M3 X 8MM 18-8 Stainless Steel Socket Head Screw | 6
26 | 91292A132 | M4 X 40MM 18-8 Stainless Steel Socket Head Screw | 4
27 | 92673A113 | 1/4-20 18-8 Stainless Steel Hex Nut | 1
28 | 91274A160 | 1/4-20 X 5/8" Zinc-Aluminum-Coated Alloy Steel Socket Head Screw | 1

29 | INSERT_PUSH_DOWN | PUSH DOWN BRACKET THREAD COVER (3D PRINTED) | 4
30 | INSERT_CENTER_PUSH_DOWN | CENTER BASE 1/4-20 SCREW COVER (3D PRINTED) | 1

NOTE:
1. FOR ANDROID APP. INSTALLATION, SEE SEPARATE SOFTWARE INSTALLATION DOCUMENTATION
2. ALL 3D PRINT PARTS MUST BE PRINTED WITH ABS FILAMENT MATERIAL
3. ESP32 BOARD ASSEMBLY DRAWING IS CURRENTLY NOT AVAILABLE
4. BE EXTRA CAREFUL WHEN APPLYING SUPER GLUE AROUND SCREW & NUT THREAD
5. CAMERA TRIPOD MAY NOT BE COMPATIBLE WITH OTHER MODEL THAN VPT-120SE TRIPOD
6. USER TO PROVIDE AN ANDROID BASED SMART PHONE IS NOT PROVIDED
7. USER TO PROVIDE M3 & M4 SIZE ALLEN WRENCH
8. USER TO PROVIDE 1/4-20 SOCKET WRENCH

UNLESS OTHERWISE SPECIFIED: | | | DATE | BYU-IDAHO ECEN 499 TEAM E NAME
DIMENSIONS ARE IN INCHES TOLERANCES: N/A FRACTIONAL: N/A ANGULAR: N/A BEND: N/A TWO PLACE DECIMAL: N/A THREE PLACE DECIMAL: N/A | DRAWN | HC | 03-27-2022

CHECKED | | | TITLE: IMAGE RECOGNITION & TRACKING PAN AND TILT CAMERA

ENG APPR.
MFG APPR.

INTERPRET GEOMETRIC TOLERANCING PER: | Q.A.
MATERIAL ABS | | SIZE D | DWG. NO. BYUIE-0327 | REV A

PROPRIETARY AND CONFIDENTIAL
THE INFORMATION CONTAINED IN THIS
DRAWING IS THE SOLE PROPERTY OF
<BYU-IDAHO ECEN 499 TEAM E>. ANY
REPRODUCTION IN PART OR AS A WHOLE
WITHOUT THE WRITTEN PERMISSION OF
<BYU-IDAHO ECEN 499 TEAM E> IS
PROHIBITED.

NEXT ASSY | USED ON | N/A FINISH

SOLIDWORKS Educational Product. For Instructional Use Only.

APPLICATION | DO NOT SCALE DRAWING | | SCALE: 1:4 | WEIGHT: | SHEET 1 OF 9

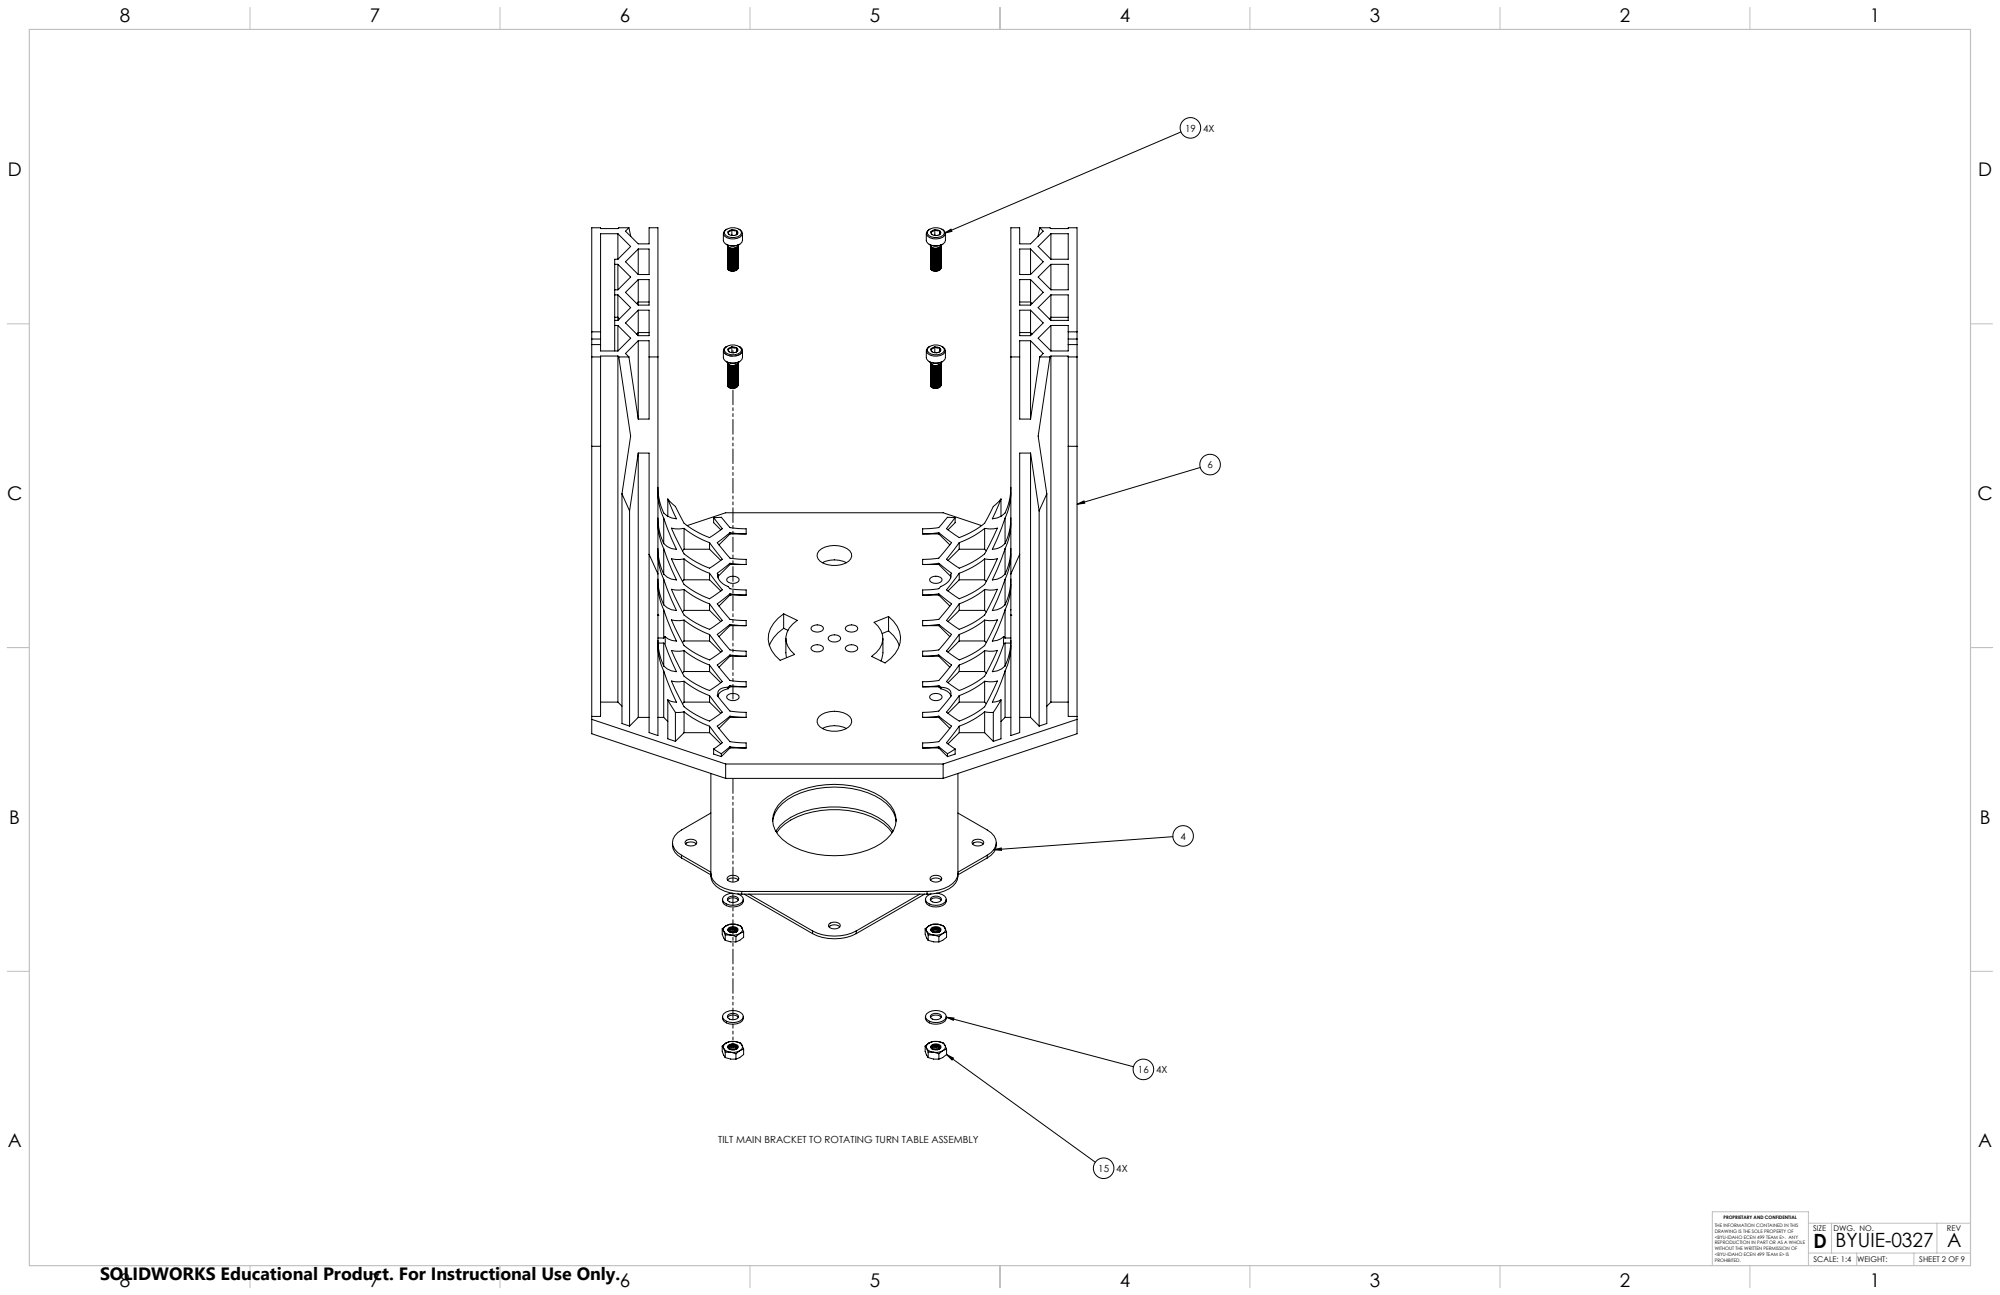
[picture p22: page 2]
TILT MAIN BRACKET TO ROTATING TURN TABLE ASSEMBLY

BYUIE-0327 | A

SCALE: 1:4 | WEIGHT: | SHEET 2 OF 9

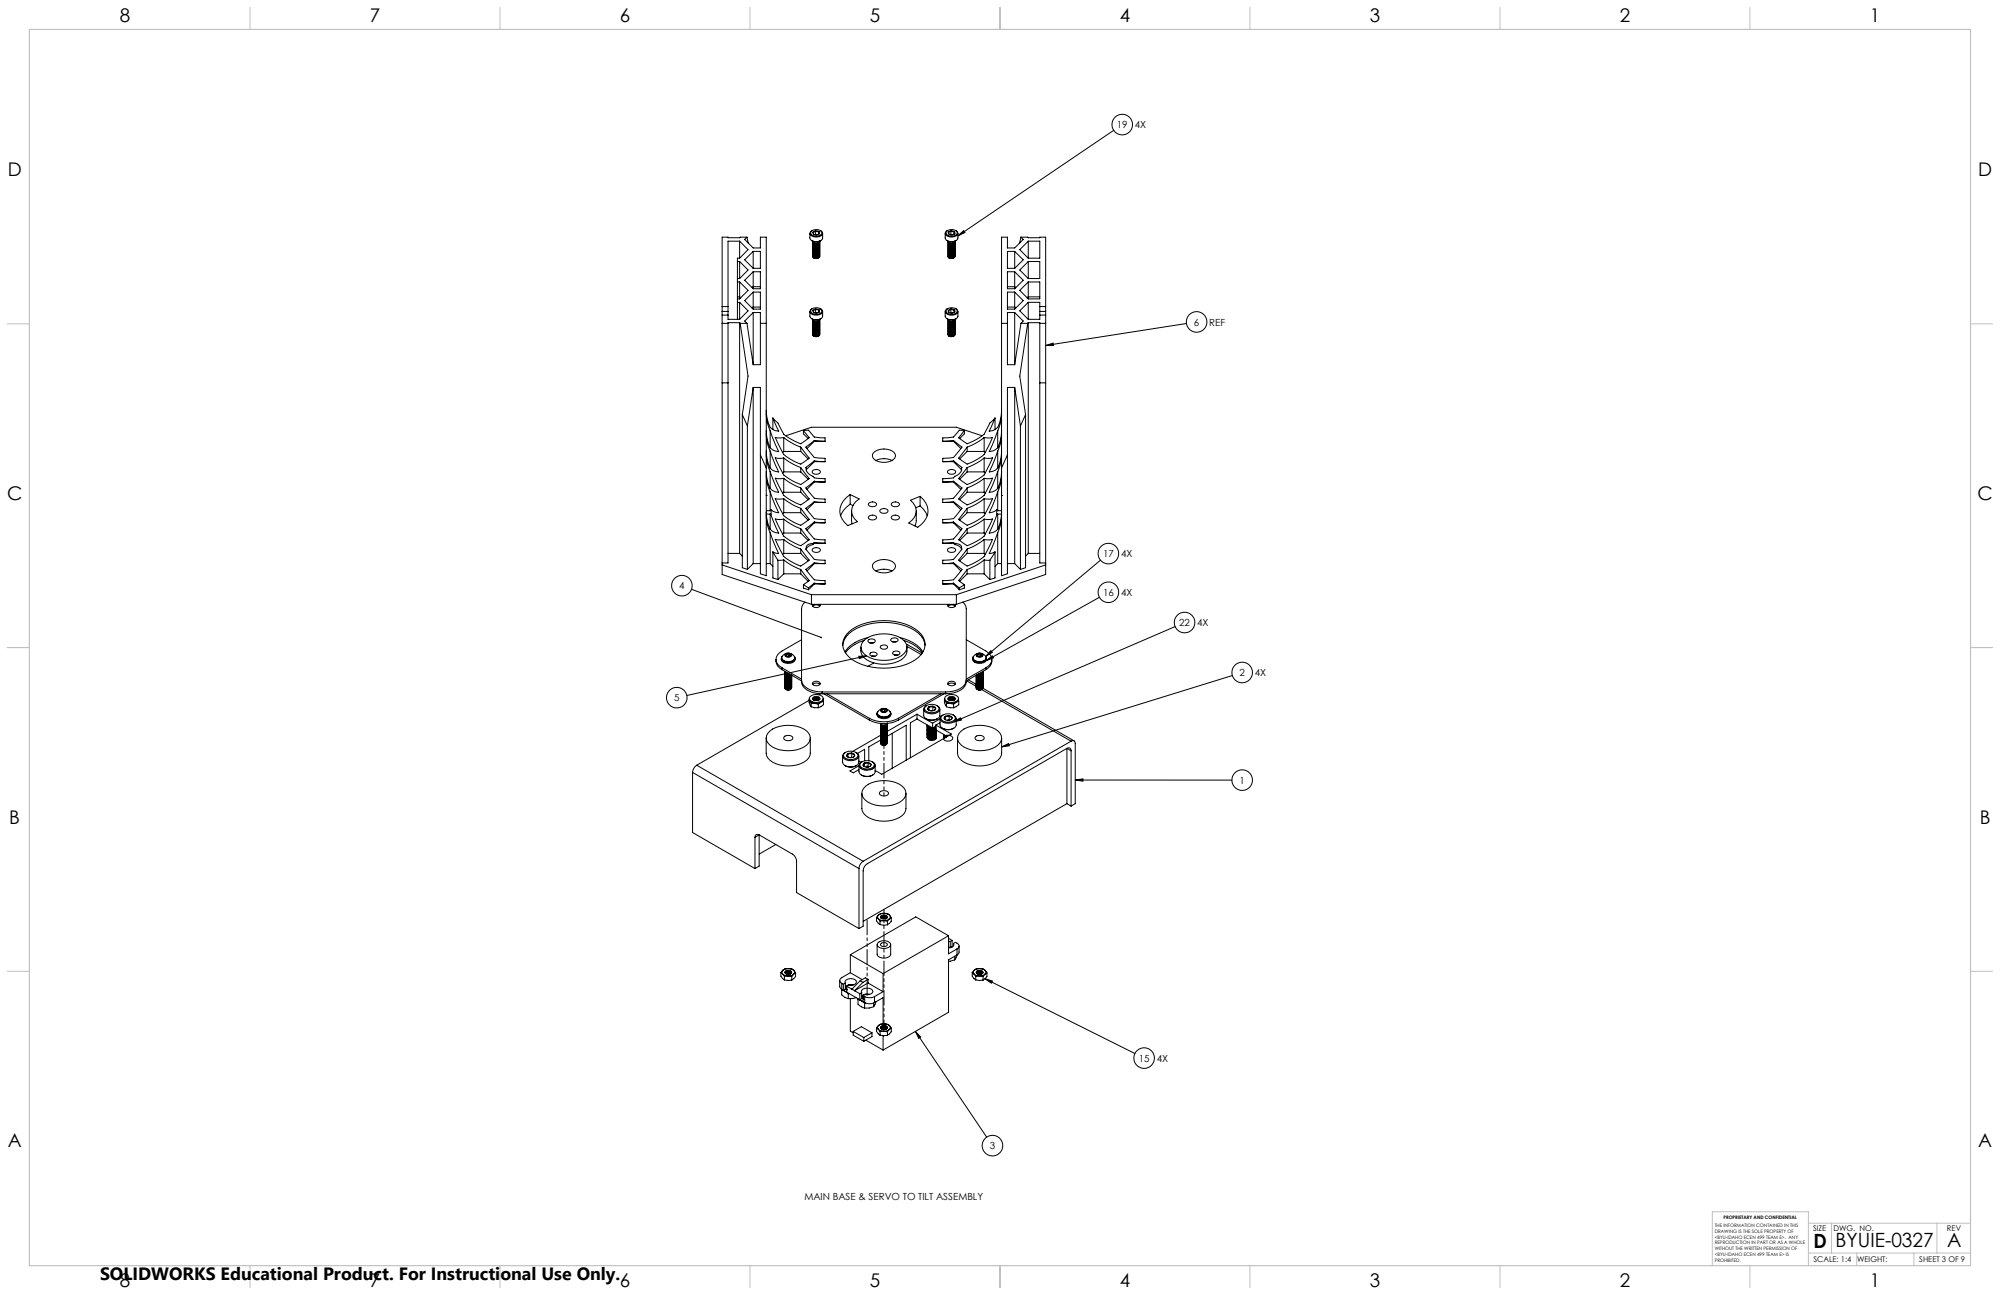
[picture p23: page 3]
6 REF

MAIN BASE & SERVO TO TILT ASSEMBLY

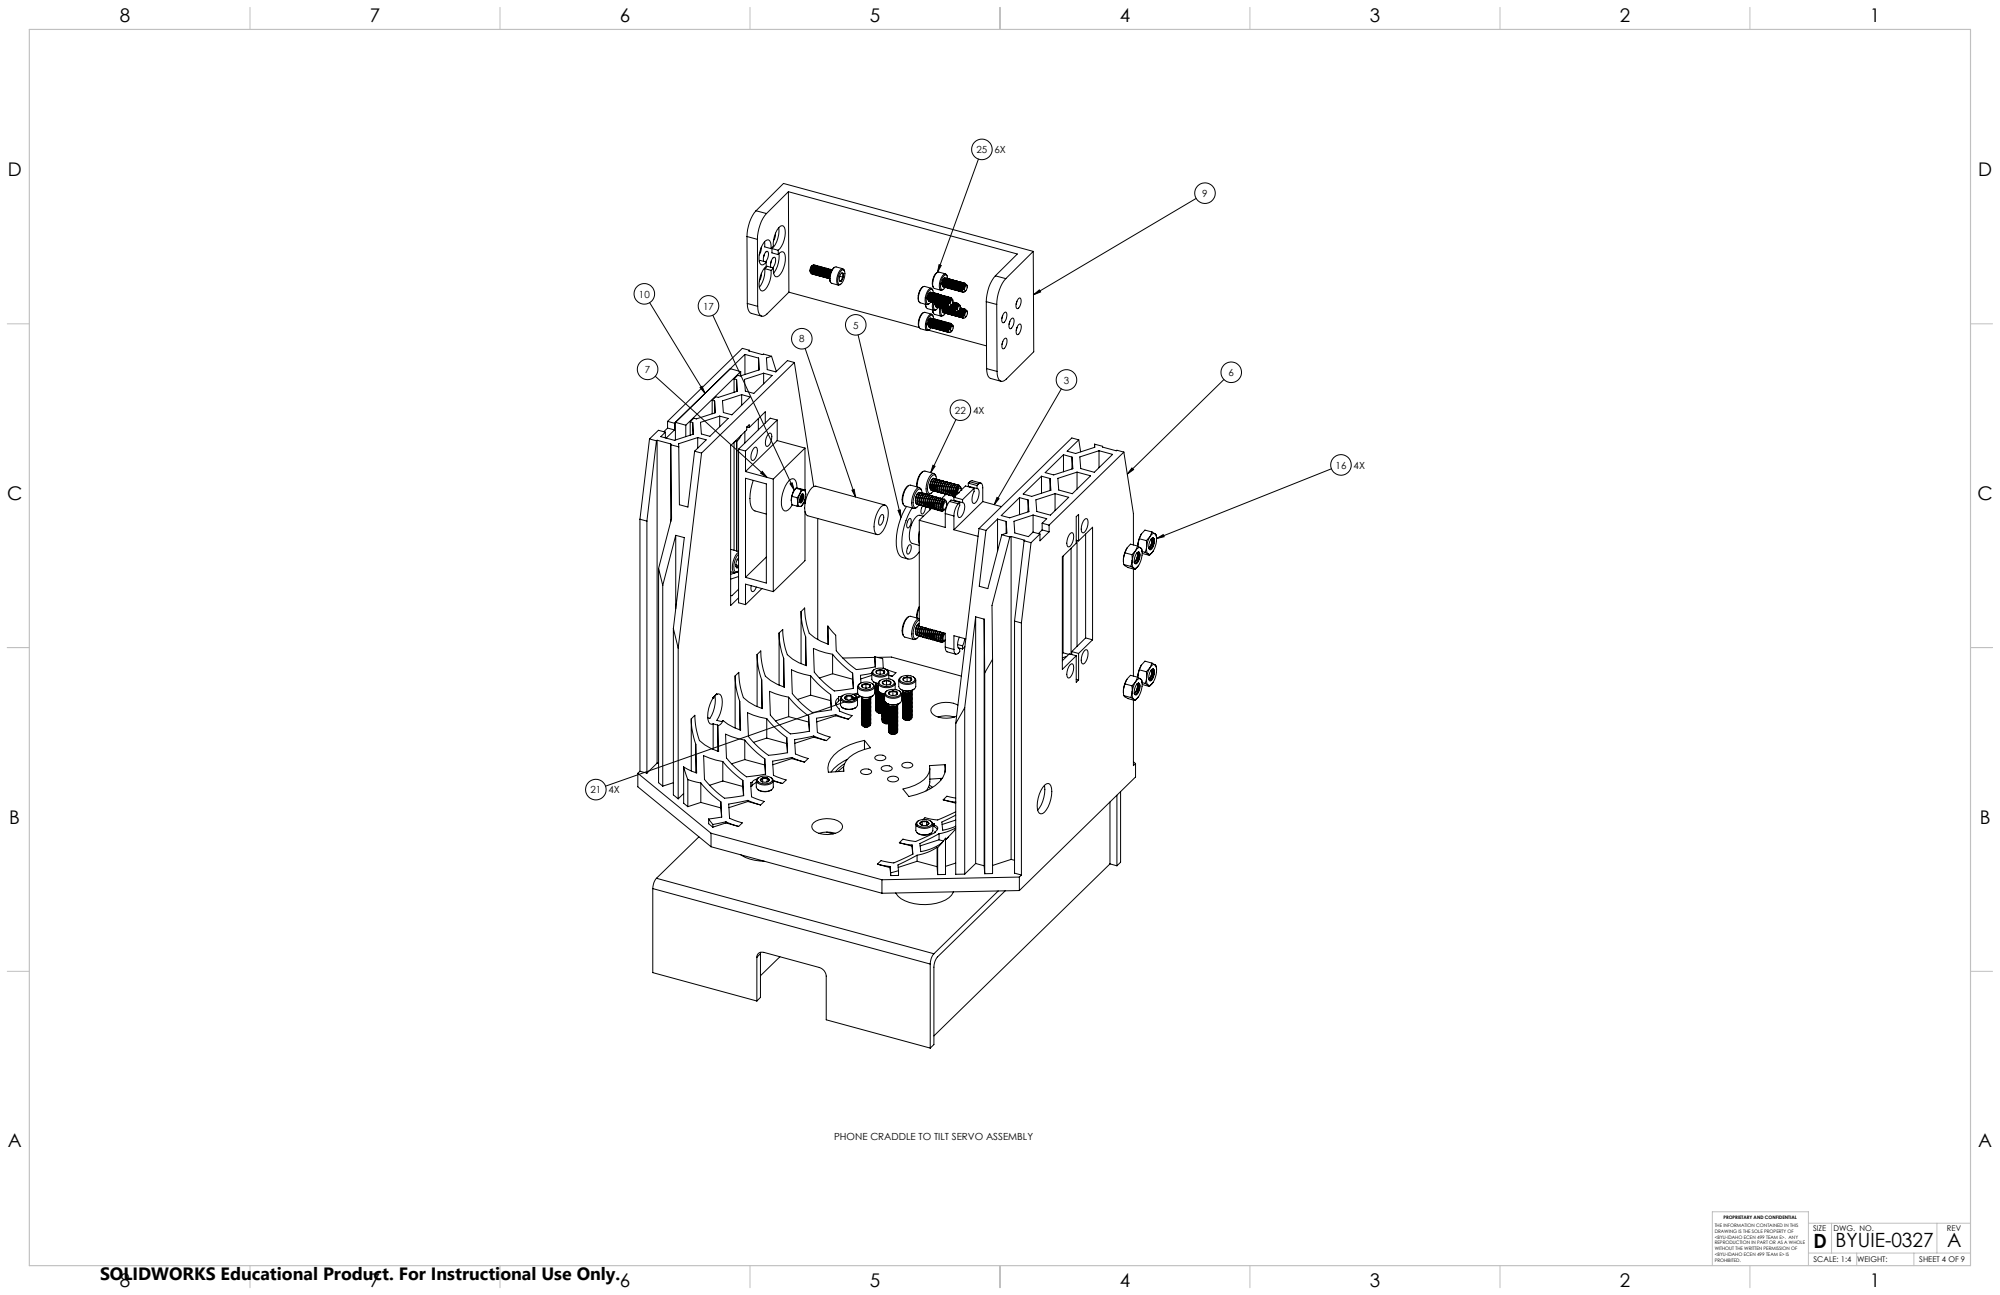
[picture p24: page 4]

PHONE CRADDLE TO TILT SERVO ASSEMBLY

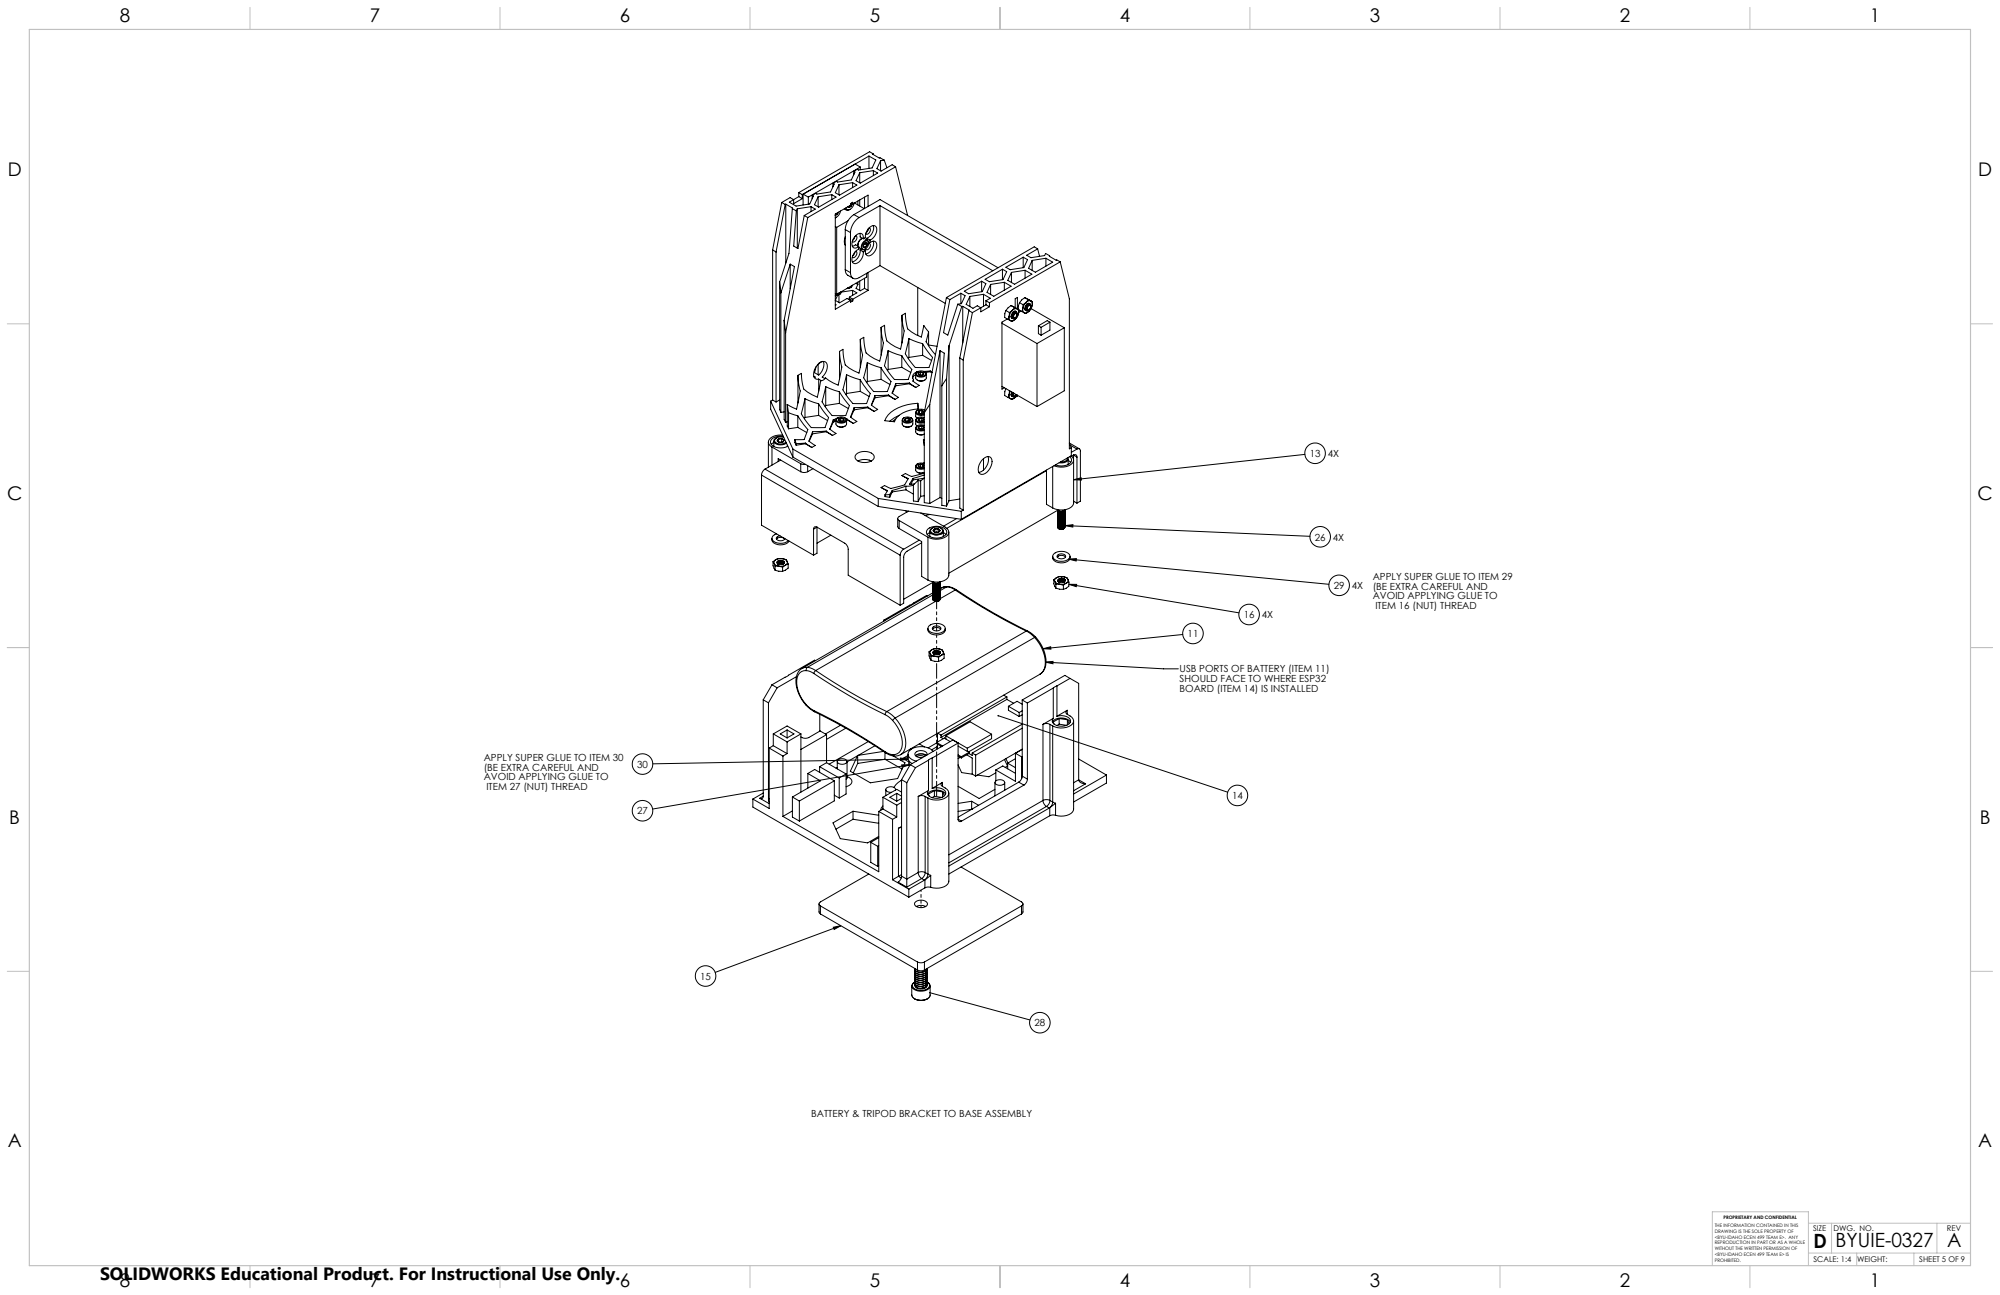
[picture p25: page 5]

APPLY SUPER GLUE TO ITEM 29
(BE EXTRA CAREFUL AND
AVOID APPLYING GLUE TO
ITEM 16 (NUT) THREAD

USB PORTS OF BATTERY (ITEM 11)
SHOULD FACE TO WHERE ESP32
BOARD (ITEM 14) IS INSTALLED

APPLY SUPER GLUE TO ITEM 30
ITEM 27 (NUT) THREAD

BATTERY & TRIPOD BRACKET TO BASE ASSEMBLY

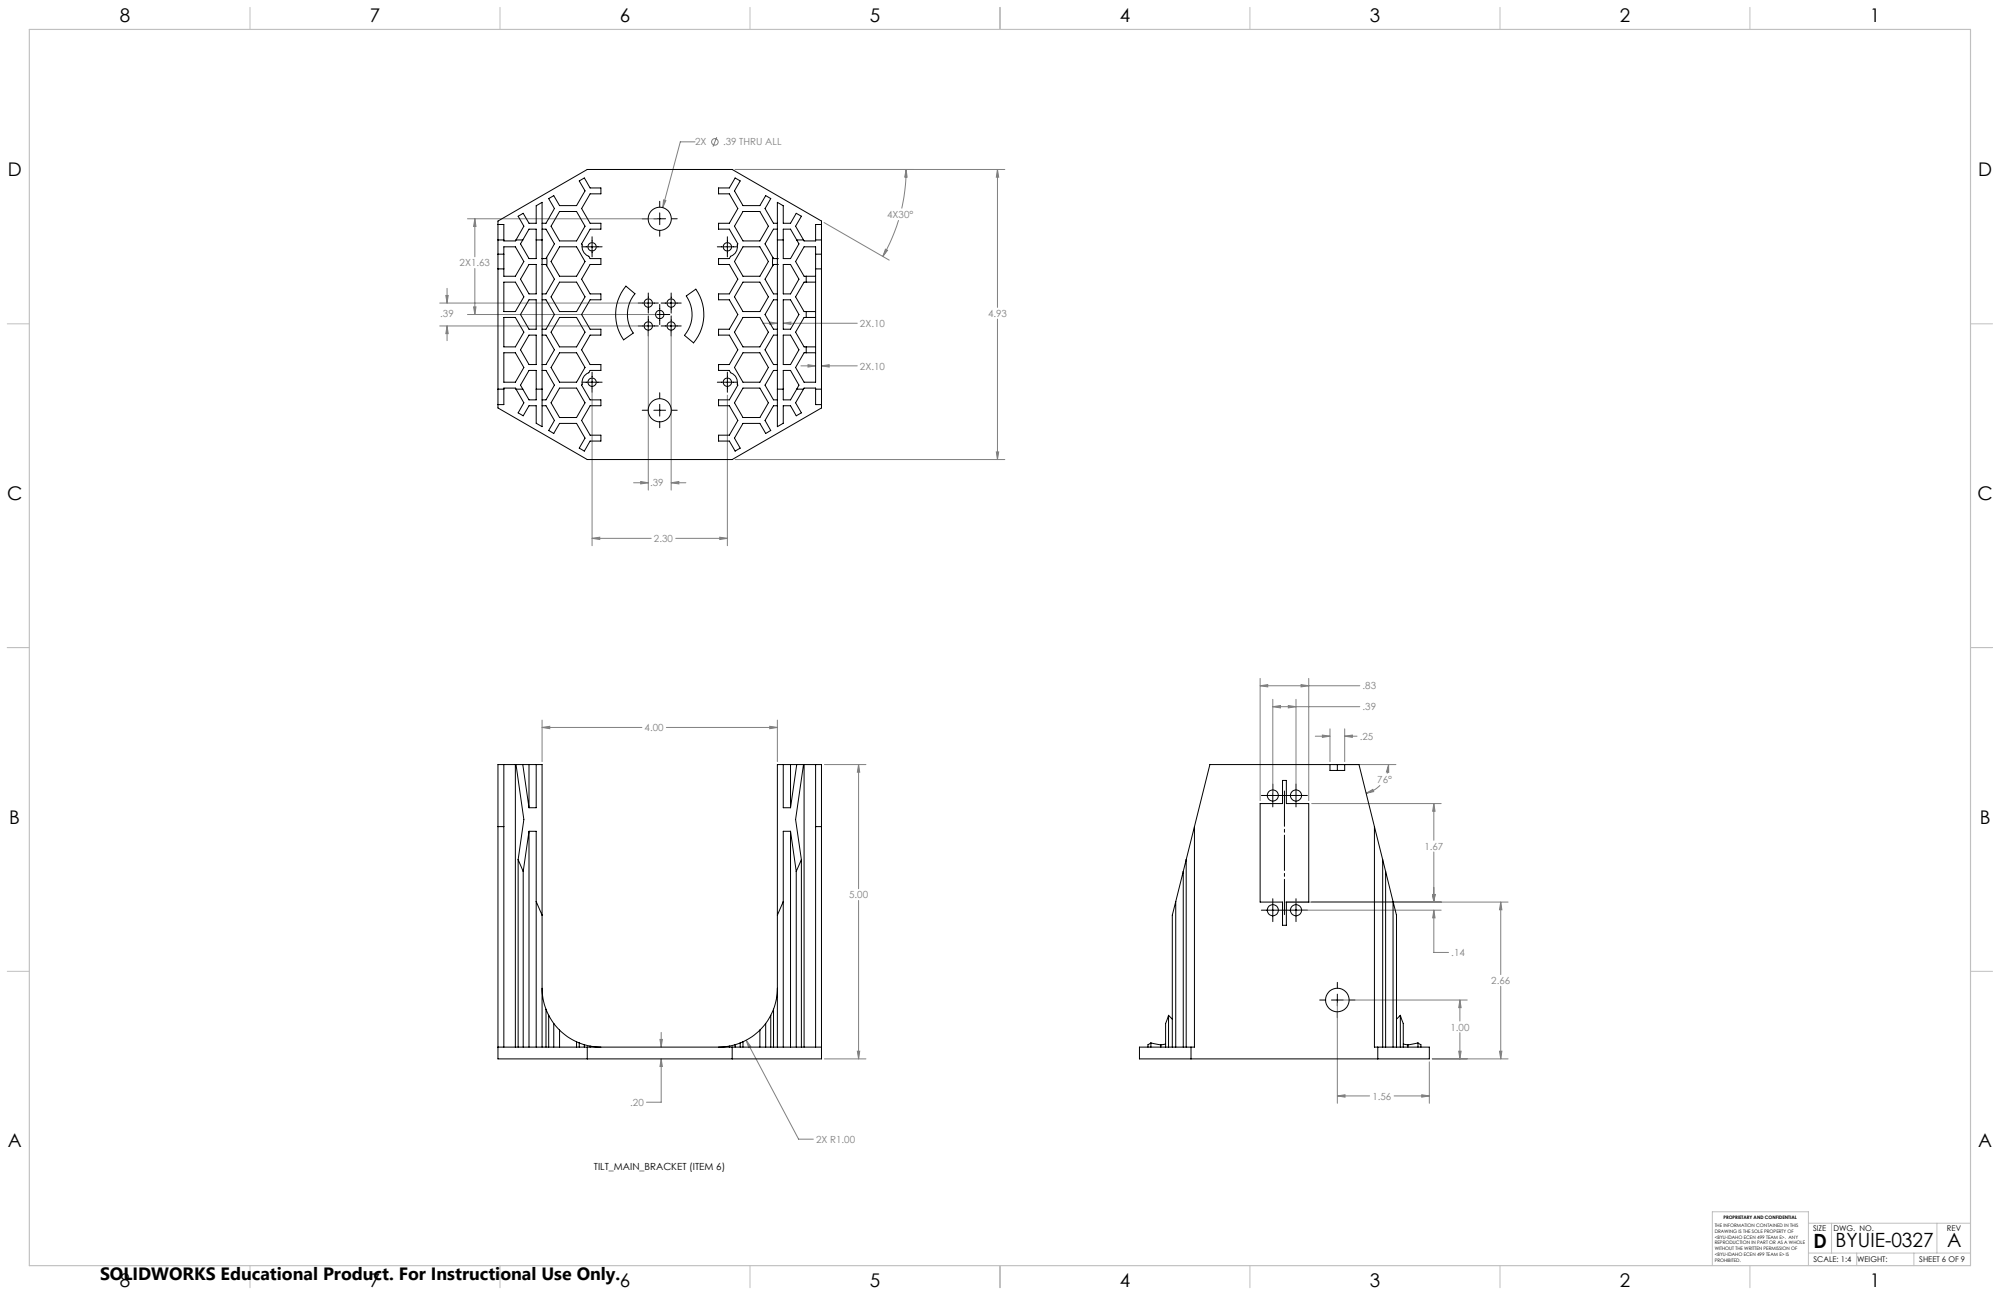
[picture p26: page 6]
.39 THRU ALL; TILT_MAIN_BRACKET (ITEM 6)

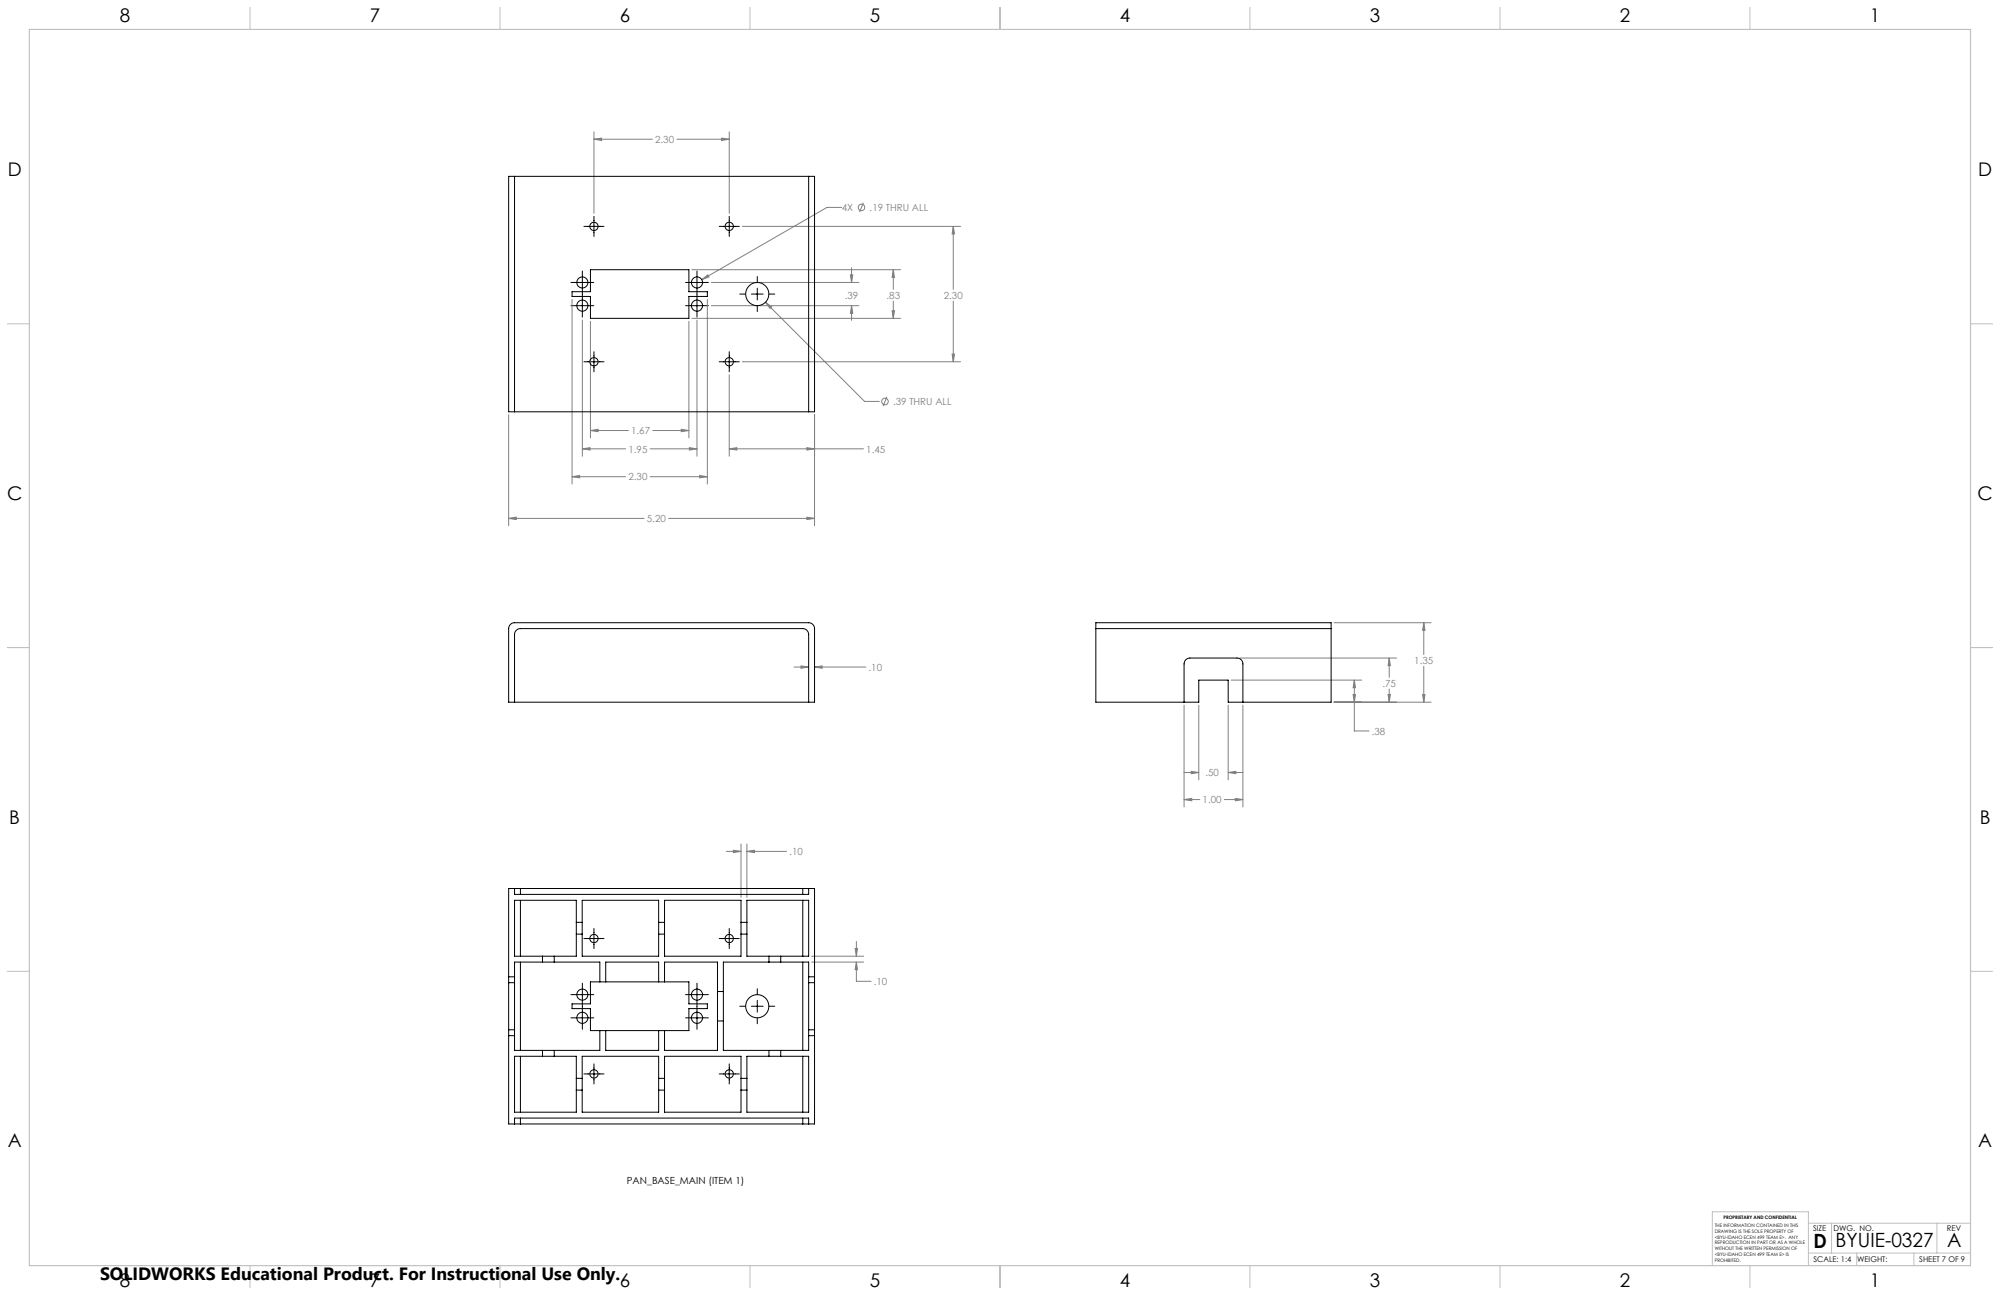
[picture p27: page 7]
.39 THRU ALL; .19 THRU ALL; PAN_BASE_MAIN (ITEM 1)

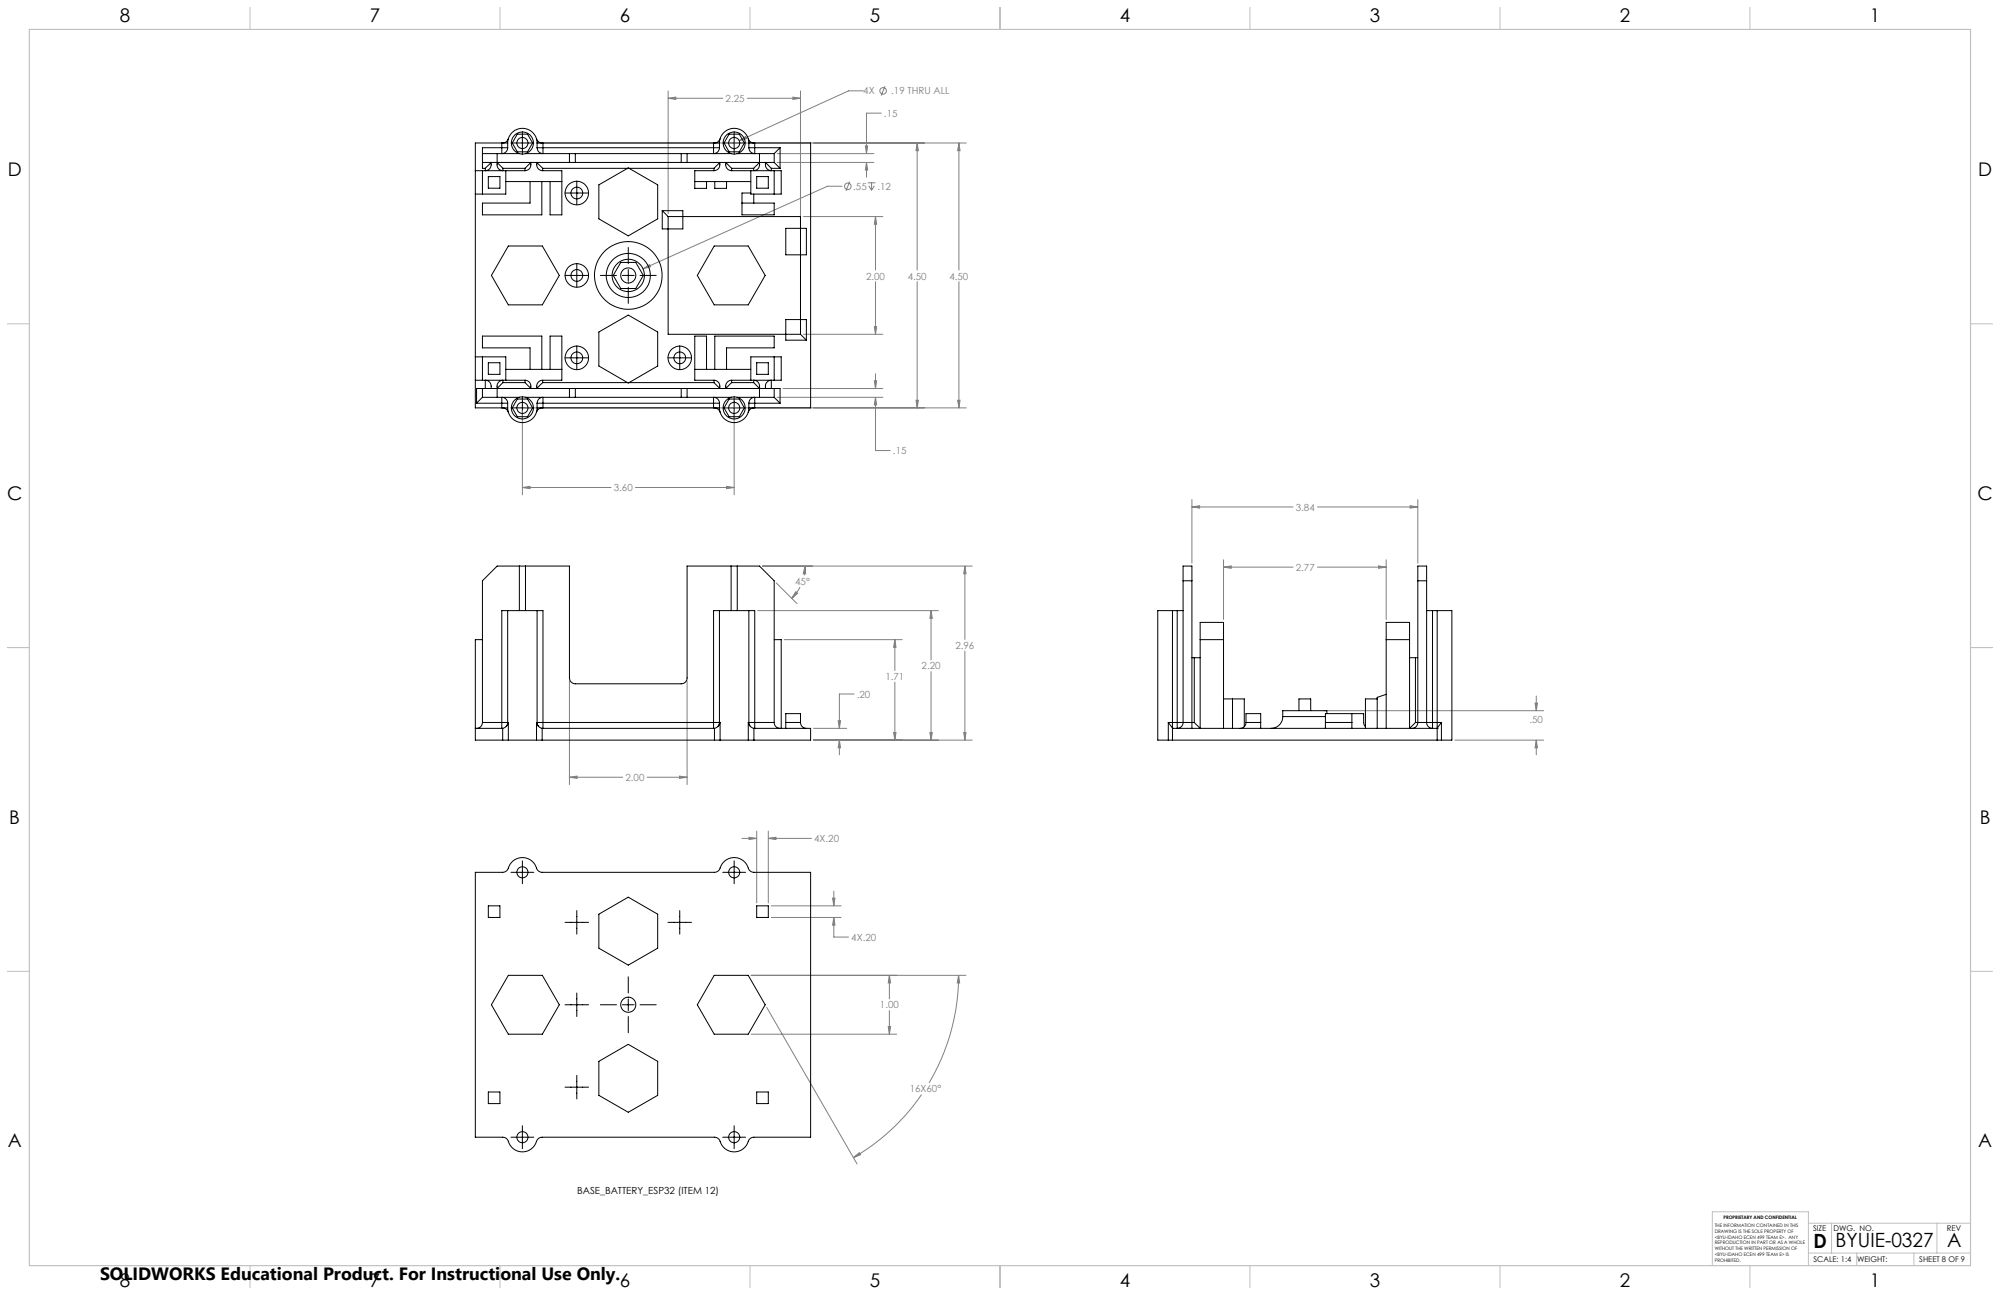
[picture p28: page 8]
.19 THRU ALL; BASE_BATTERY_ESP32 (ITEM 12)

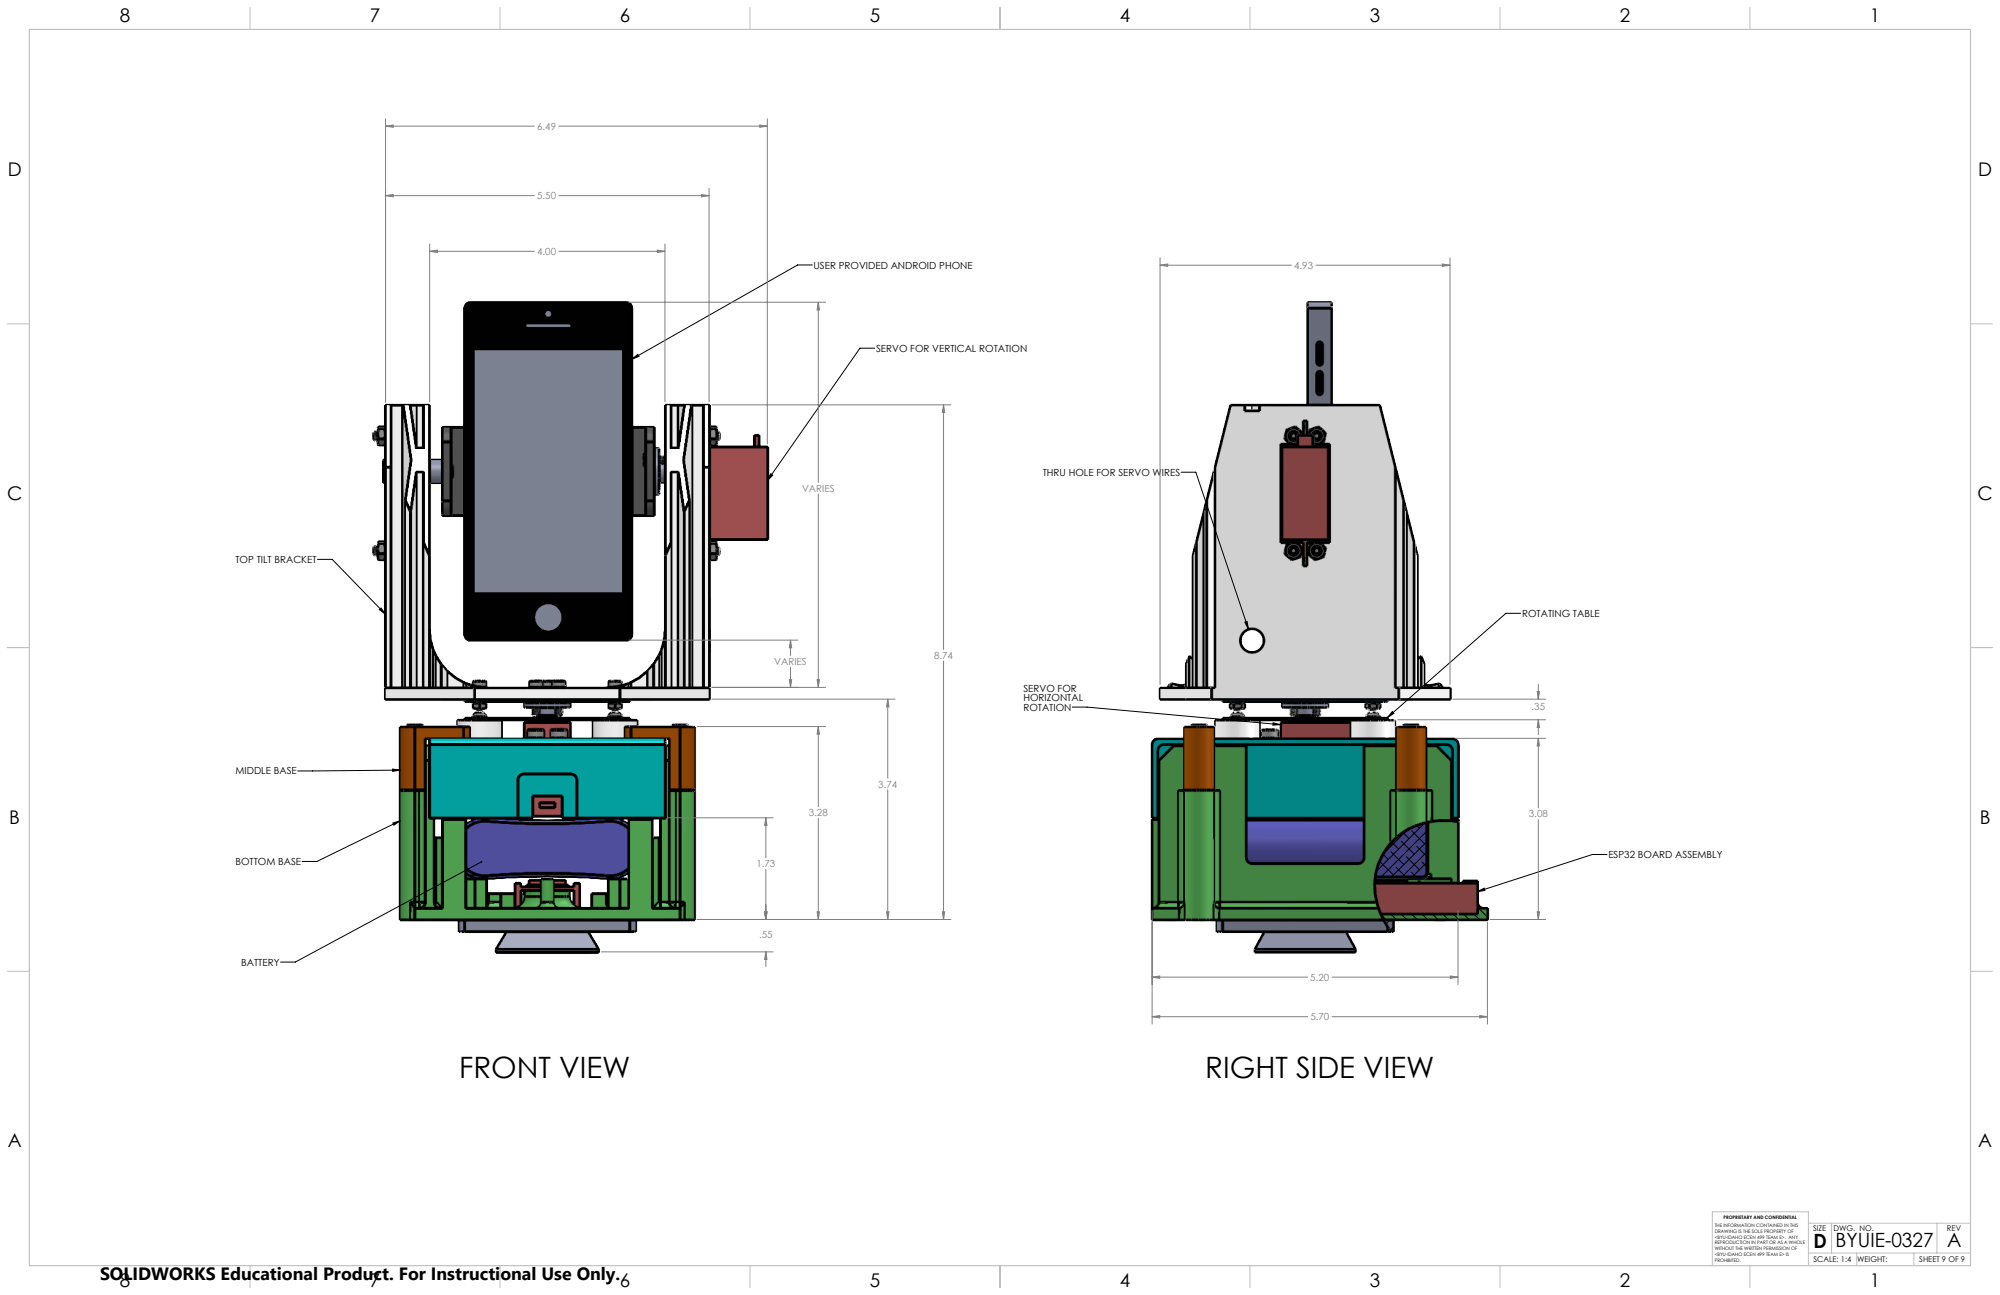
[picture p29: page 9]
FRONT VIEW; BOTTOM BASE; MIDDLE BASE; ESP32 BOARD ASSEMBLY; ROTATING TABLE; SERVO FOR

USER PROVIDED ANDROID PHONE

SERVO FOR VERTICAL ROTATION

THRU HOLE FOR SERVO WIRES

TOP TILT BRACKET

RIGHT SIDE VIEW

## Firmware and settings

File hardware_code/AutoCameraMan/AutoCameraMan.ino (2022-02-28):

//For a better understanding of the bluetooth code go to https://randomnerdtutorials.com/esp32-bluetooth-classic-arduino-ide/

#include "BluetoothSerial.h"
#include <Servo_ESP32.h>
#define tiltServoPin 18
#define panServoPin 5
#if !defined(CONFIG_BT_ENABLED) || !defined(CONFIG_BLUEDROID_ENABLED)
#error Bluetooth is not enabled! Please run `make menuconfig` to and enable it
#endif

BluetoothSerial SerialBT;
//static const int tiltServoPin = 18; //printed 18 on the board
//static const int panServoPin = 5; //printed 5 on the board
Servo_ESP32 tiltServo, panServo;
int panAngle = 90;
int prevPanAngle =90;
int tiltAngle = 0;
int prevTiltAngle = 0;
int angleStep = 1;
int angleMin = 0;
int angleMax = 180;
 
void setup() {
  Serial.begin(115200);
  SerialBT.begin("AutoCameraMan"); //Bluetooth device name
  tiltServo.attach(tiltServoPin); 
  panServo.attach(panServoPin);
  
  panServo.write(0);
  delay(1000);
  panServo.write(270);
  delay(1000);
  panServo.write(panAngle);
  delay(1000);
  
}
 
void loop() {
  //panRight();
  //panLeft();
  //tiltUp();
  //tiltDown();
  
  //Send data back to the app but be aware
  //nothing has been configured on the app
  //to receive or process data from the ESP32
  /*if (Serial.available()) {
    SerialBT.write(Serial.read());
  }*/
  
  // Receive data
  if (SerialBT.available()) {
    //Serial.write(SerialBT.read());
    char getstr = SerialBT.read();
    switch(getstr) {
      case '0': panRight(); break;
      case '1': panLeft();break;
      case '2': tiltUp(); break;
      case '3': tiltDown(); break;
      default:  break;
    }
  }
  if (prevPanAngle != panAngle){
  panServo.write(panAngle);
  Serial.println(panAngle);
  tiltServo.write(tiltAngle);
  }
}


void tiltUp()
{
   /*for(int tiltAngle = 0; tiltAngle <= angleMax; tiltAngle +=angleStep) {
        tiltServo.write(tiltAngle);
        //Serial.println(angle);
        delay(20);
    }*/

    //Going to need to find out what the sweet spot is for the angle range. Maybe 90
    Serial.println("tiltDown");
    if (tiltAngle < 180) {
      tiltAngle += angleStep;
    }
    
}

void tiltDown()
{
  /*for(int tiltAngle = 180; tiltAngle >= angleMin; tiltAngle -=angleStep) {
        tiltServo.write(tiltAngle);
        //Serial.println(angle);
        delay(20);
    }*/

    Serial.println("tiltDown");
    if (tiltAngle > 0) {
      tiltAngle -= angleStep;
    }
}

void panRight()
{
   /*for(int panAngle = 0; panAngle <= angleMax; panAngle +=angleStep) {
        panServo.write(panAngle);
        delay(20);
    }*/

    // Want to get a full 270 degrees out of pan
    Serial.println("panRight");
    if (panAngle < 180) {
      prevPanAngle = panAngle;
      panAngle += angleStep;
    }
}

void panLeft()
{
  /*for(int panAngle = 180; panAngle >= angleMin; panAngle -=angleStep) {
        panServo.write(panAngle);
        delay(20);
    }*/
    Serial.println("panLeft");
    if (panAngle > 0) {
      prevPanAngle = panAngle;
      panAngle -= angleStep;
    }
}

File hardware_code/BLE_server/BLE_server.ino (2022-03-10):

/*
    Based on Neil Kolban example for IDF: https://github.com/nkolban/esp32-snippets/blob/master/cpp_utils/tests/BLE%20Tests/SampleServer.cpp
    Ported to Arduino ESP32 by Evandro Copercini
    updates by chegewara
*/

#include <BLEDevice.h>
#include <BLEUtils.h>
#include <BLEServer.h>

// See the following for generating UUIDs:
// https://www.uuidgenerator.net/

#define SERVICE_UUID        "4fafc201-1fb5-459e-8fcc-c5c9c331914b"
#define CHARACTERISTIC_UUID "beb5483e-36e1-4688-b7f5-ea07361b26a8"

void setup() {
  Serial.begin(115200);
  Serial.println("Starting BLE work!");

  BLEDevice::init("BLE_CameraMan");
  BLEServer *pServer = BLEDevice::createServer();
  BLEService *pService = pServer->createService(SERVICE_UUID);
  BLECharacteristic *pCharacteristic = pService->createCharacteristic(
                                         CHARACTERISTIC_UUID,
                                         BLECharacteristic::PROPERTY_READ |
                                         BLECharacteristic::PROPERTY_WRITE
                                       );

  pCharacteristic->setValue("Hello World says Neil");
  pService->start();
  // BLEAdvertising *pAdvertising = pServer->getAdvertising();  // this still is working for backward compatibility
  BLEAdvertising *pAdvertising = BLEDevice::getAdvertising();
  pAdvertising->addServiceUUID(SERVICE_UUID);
  pAdvertising->setScanResponse(true);
  pAdvertising->setMinPreferred(0x06);  // functions that help with iPhone connections issue
  pAdvertising->setMinPreferred(0x12);
  BLEDevice::startAdvertising();
  Serial.println("Characteristic defined! Now you can read it in your phone!");
}

void loop() {
  // put your main code here, to run repeatedly:
  delay(2000);
}

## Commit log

2022-01-16 Added basic functionality that allows access to the camera and displays the live feed to the screen
2022-01-25 deleted current app project
2022-01-25 Added ML kit
    [fitness_pose_samples.csv]
2022-01-25 ml kit
    [fitness_pose_samples.csv]
2022-01-25 put project in image_recog instead of vision
    [fitness_pose_samples.csv]
2022-01-26 built the project
    [fitness_pose_samples.csv]
2022-01-26 initialize project
    [fitness_pose_samples.csv]
2022-01-30 added record button
2022-02-02 updated ESP32 bluetooth code
2022-02-07 Made BT device names visible
2022-02-08 added servo control on ESP32
2022-02-09 removing build files
    [fitness_pose_samples.csv]
2022-02-09 build file push test
    [fitness_pose_samples.csv]
2022-02-09 removed build again
    [fitness_pose_samples.csv]
2022-02-09 fixed bluetooth bug in livepreviewactivity
    [LivePreviewActivity.kt]
2022-02-09 build files test
    [fitness_pose_samples.csv]
2022-02-09 removed build files
    [fitness_pose_samples.csv]
2022-02-14 Added record video intent to record button
2022-02-15 code sends moving instructions to board
2022-02-16 updated servo code
2022-02-20 Pose detection now sends the correct motor control data over bluetooth
    [AutoCameraMan.ino, FaceGraphic.kt, LivePreviewActivity.kt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]
2022-03-02 Added ios_image_recognition folder and changed image_recognition to android_image_recognition
    [fitness_pose_samples.csv]
2022-03-02 updates to repo
    [fitness_pose_samples.csv]
2022-03-02 Added android doc link for camera usage
2022-03-10 changed folder names to just android and ios
    [fitness_pose_samples.csv]
2022-03-19 removed the extra button on the main activity
2022-03-23 Bux fix for recording
    [LivePreviewActivity.kt]
2022-03-28 fixed Pan & Tilt for front & back camera
    [FaceGraphic.kt, PoseGraphic.kt]
2022-04-01 removed work around button
2022-04-04 Adding fasteners
    [1 4 -20 5 AND 8_Zinc-Aluminum-Coated Alloy Steel Socket Head Screw_91274A160.SLDPRT, 1 4 -20_18-8 Stainless Steel Hex Nut_92673A113.SLDPRT, M3 X 10MM_18-8 Stai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]
2022-04-04 Adding main assembly files
    [20KG_6.8V_8V_DIGITAL_SERVO_DSSERVO.SLDDRW, 20KG_6.8V_8V_DIGITAL_SERVO_DSSERVO.SLDPRT, BASE_1.3.SLDDRW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]
2022-04-04 Moved solidworks files
    [1 4 -20 5 AND 8_Zinc-Aluminum-Coated Alloy Steel Socket Head Screw_91274A160.SLDPRT, 1 4 -20_18-8 Stainless Steel Hex Nut_92673A113.SLDPRT, 20KG_6.8V_8V_DIGITA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]
2022-04-04 Adding Prototype 1.0 SolidWorks files
2022-04-04 Adding Prototype 1.1 SolidWorks files
2022-04-04 Adding Prototype 2.0 SolidWorks files
2022-04-04 Adding Prototype 2.1 SolidWorks files
2022-04-05 Development CAD files
2022-04-06 added servo libaries folder
